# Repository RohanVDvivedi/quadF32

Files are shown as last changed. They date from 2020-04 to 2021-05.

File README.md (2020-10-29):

# Flight controller using STM32F103
[Documentation and demonstration video link](https://youtu.be/UyUF_jVTML4)

### setup requirements
(for programming stm32f103 microcontroller)

* Linux debian (to use make build system and code upload tool stm32flash)
* sublime/vi/vim/gedit any texteditor
* ARM cross compiler toolchain
  * sudo apt-get install gcc-arm-none-eabi binutils-arm-none-eabi
* stm32flash to flash the controller, assuming the controller has default factory bootloader
  * sudo apt-get install stm32flash
* stm32f103 microcontroller, with default factory bootloader (must)
* usb to uart converter
  * PL2303HX, CP2102, ftdi etc

### sensors
 * mpu6050  sccelerometer and gyroscope
 * hmc5883l magnetometer
 * ms5611 barometer

### additional accessories
 * rc transmitter and receiver

#### [STM32F10x Reference Manual](https://www.st.com/resource/en/reference_manual/cd00171190-stm32f101xx-stm32f102xx-stm32f103xx-stm32f105xx-and-stm32f107xx-advanced-arm-based-32-bit-mcus-stmicroelec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)

### connections (from microcontroller)
 * I2c1 {PB6, PB7} -> GY86 sensor {SCL, SDA}
 * UART1 {PA10, PA9} -> UART debug port {RX, TX}
 * {PB10, PB11, PB12, PB13, PB14, PB15} -> RC receiver
 * {PA0, PA1, PA2, PA3} -> PWM to ESCs of corresponding motors (Left Front, Right Front, Left Back, Right Back) of Quadcopter
 
### PCB designs
 * You will find the .sch and .brd, QuadF32 flight controller board designs in the Eagle_CAD folder.
 * It would also include a generated .cam file that I used for building my board, I would request you to use a different cam file provided by your pcb manufacturer.
 * The folder also does include .lbr library for the stm32f103 module, that I am using.

### Third party acknowledgements
 * [STM32F103-c8t6 eagle cad library](https://os.mbed.com/users/hudakz/code/STM32F103C8T6_Hello/file/accb2c83a007/mbed-STM32F103C8T6.lib/)

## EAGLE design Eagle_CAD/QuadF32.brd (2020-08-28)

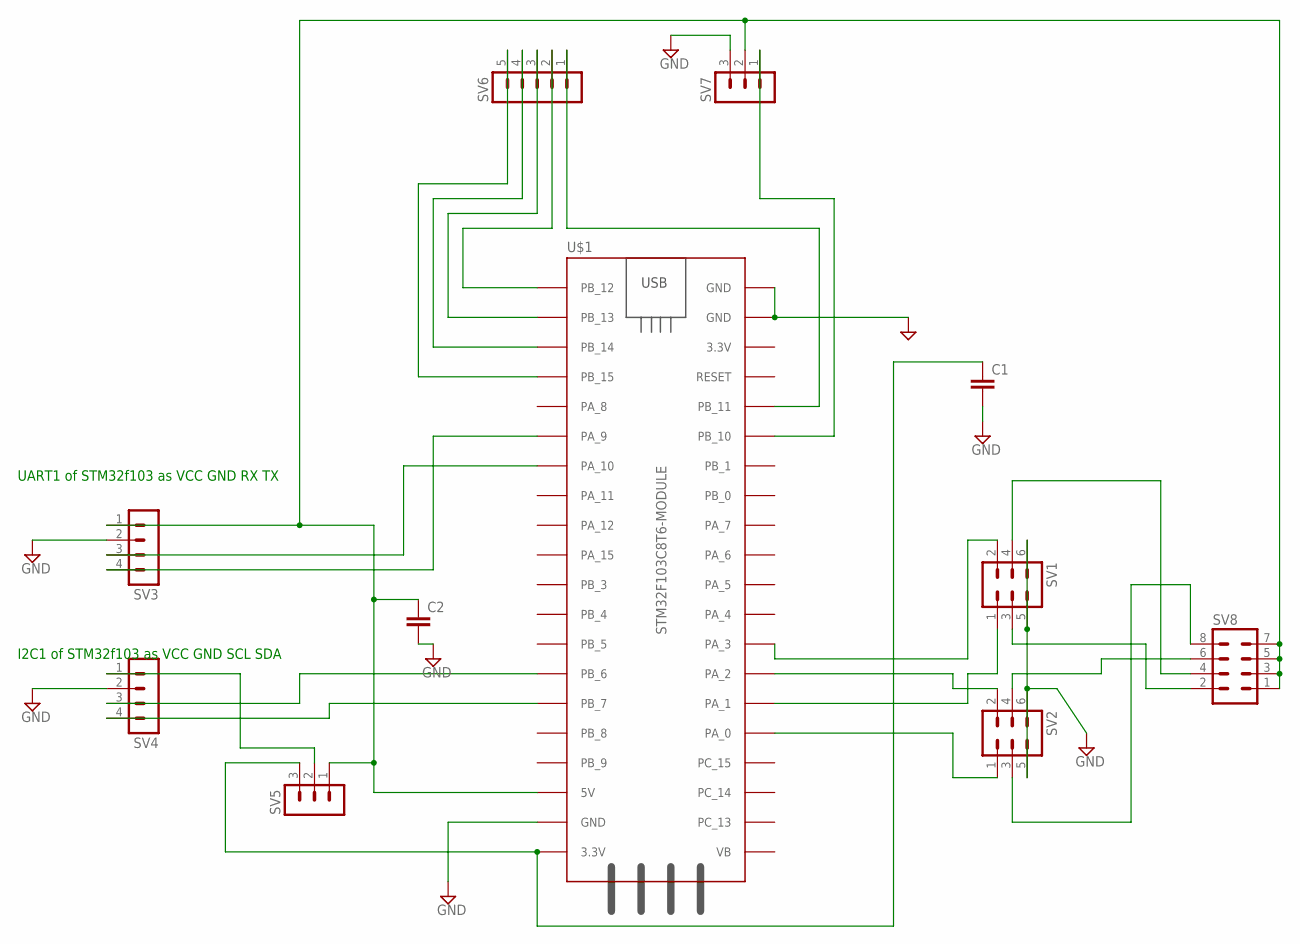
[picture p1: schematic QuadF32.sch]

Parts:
C1, C2: C5/2.5; C5B2.5
SV1, SV2: MA03-2
SV3, SV4: MA04-1
SV5, SV7: MA03-1
SV6: MA05-1
SV8: MA04-2
U$1: STM32F103C8T6-MODULE

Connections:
GND: C1.2, C2.2, SV1.5, SV1.6, SV2.5, SV2.6, SV3.2, SV4.2, SV7.3, U$1.GND_1 (GND), U$1.GND_2 (GND), U$1.GND_3 (GND)
unnamed: SV4.3, U$1.PB_6
unnamed: SV4.4, U$1.PB_7
unnamed: SV3.3, U$1.PA_10
unnamed: SV3.4, U$1.PA_9
unnamed: SV2.1, U$1.PA_0
unnamed: SV2.2, U$1.PA_2
unnamed: SV1.1, U$1.PA_1
unnamed: SV1.2, U$1.PA_3
unnamed: SV6.5, U$1.PB_15
unnamed: SV6.4, U$1.PB_14
unnamed: SV6.3, U$1.PB_13
unnamed: SV6.2, U$1.PB_12
unnamed: SV6.1, U$1.PB_11
unnamed: SV7.1, U$1.PB_10
unnamed: SV1.4, SV8.4
unnamed: C1.1, SV5.3, U$1.3.3V_1 (3.3V)
unnamed: SV4.1, SV5.2
unnamed: C2.1, SV3.1, SV5.1, SV7.2, SV8.1, SV8.3, SV8.5, SV8.7, U$1.5V
unnamed: SV2.3, SV8.8
unnamed: SV2.4, SV8.6
unnamed: SV1.3, SV8.2

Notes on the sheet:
UART1 of STM32f103 as VCC GND RX TX
I2C1 of STM32f103 as VCC GND SCL SDA

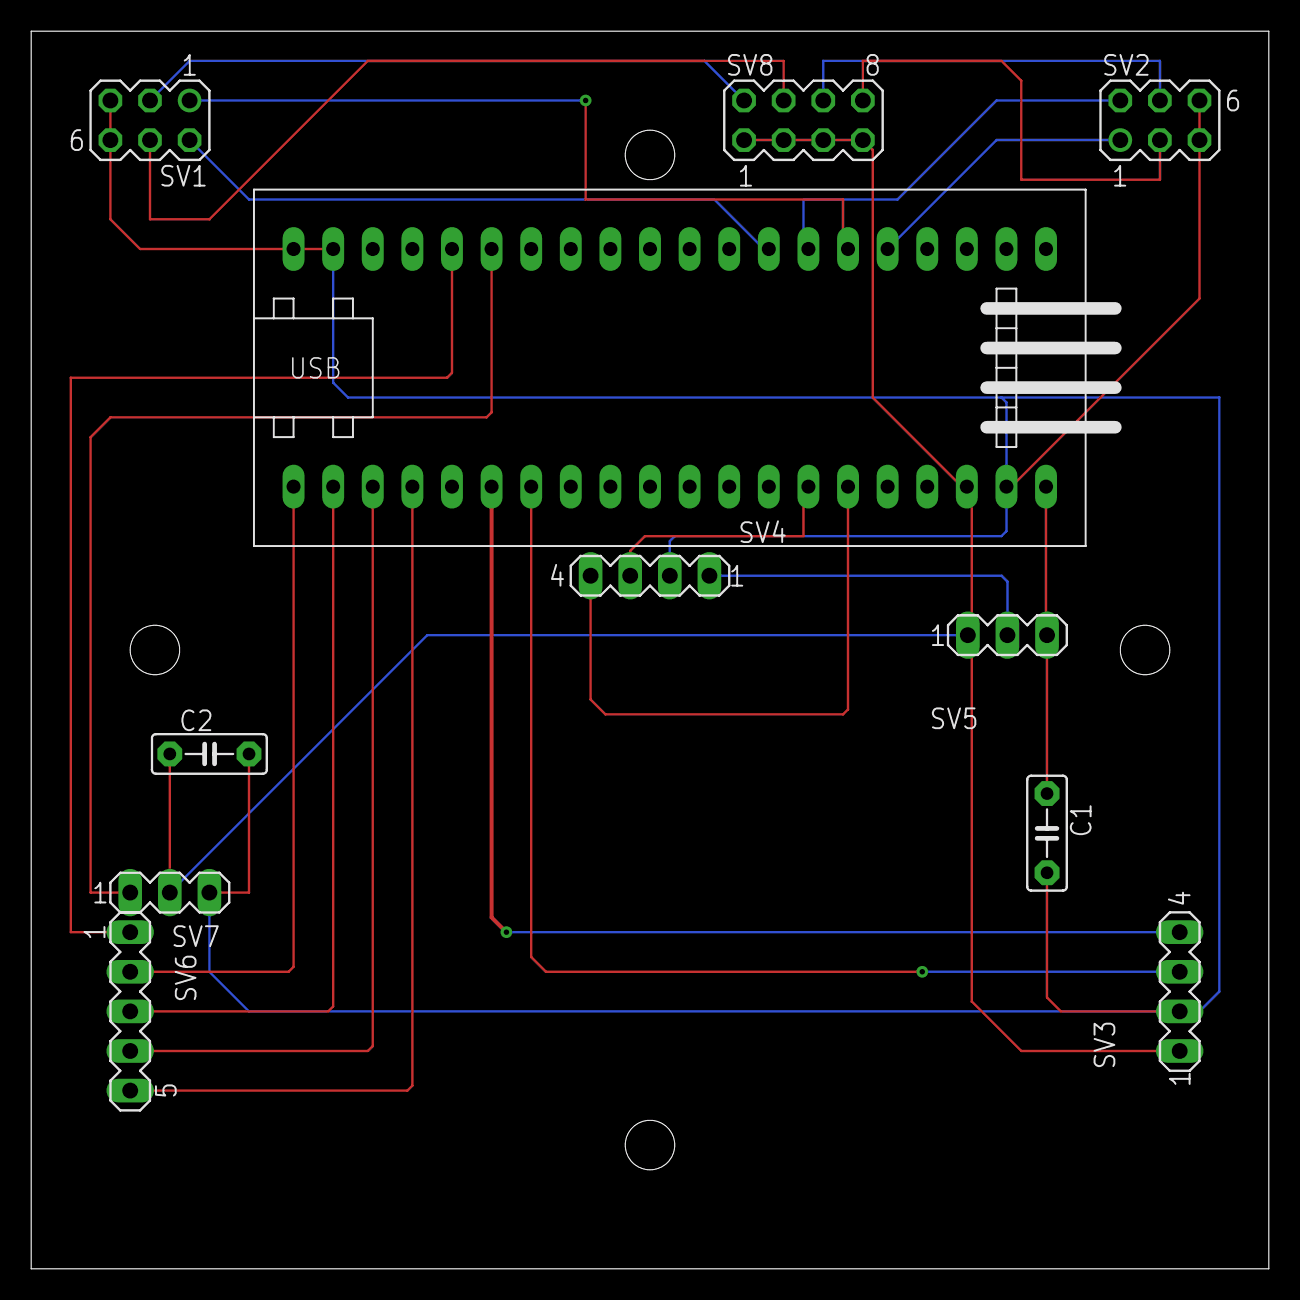
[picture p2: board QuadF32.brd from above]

Board: 2 copper layers, 79.4 x 79.4 mm, 11 parts (0 on the bottom side), 22 nets.

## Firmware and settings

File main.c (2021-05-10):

#include<delay/delay.h>
#include<d_serializer/d_serializer.h>

#include<regs/rcc.h>
#include<regs/gpio.h>

#include<sysclock/sysclock.h>
#include<uart/uart.h>
#include<i2c/i2c.h>
#include<backup_data/backup_data.h>

#include<pid/pid.h>

#include<gy86/gy86.h>
#include<bldc/quad_bldc.h>
#include<rc_receiver/rc_receiver.h>

//#define STABILIZE_MODE

#define map(val, a_min, a_max, b_min, b_max)	(b_min) + ((((float)(val)) - (a_min)) * ((b_max) - (b_min))) / ((a_max) - (a_min))

#define GYRO_ACCL_MIX     			0.98
#define LOOP_EVERY_MICROS 			2500

#define THROTTLE_MIN_VALUE			  0.0
#define THROTTLE_PID_ACTIVATE 		200.0
#define THROTTLE_MAX_VALUE			800.0

#ifdef STABILIZE_MODE
	#define ATTITUDE_INPUT_LIMIT	 30.0
#else	// it is a rate controlled quadcopter
	#define ATTITUDE_INPUT_LIMIT	120.0
#endif
#define ANGULAR_RATE_INPUT_LIMIT	120.0

#define MOTOR_MIN_PWM 				110.0
#define MOTOR_MAX_PWM 				990.0

//#define CALIBRATE_ESC_ON_START_UP

//#define DEBUG_OVER_UART
//#define PID_TO_TUNE

void main(void)
{
	// setup clock to run at 72 MHz
	change_sys_clock_source(HSE, 8000000);
	setup_pll_module(HSE, 72000000);
	change_sys_clock_source(PLL, 72000000);

	// to enable port c GPIO
	RCC->RCC_APB2ENR |= (1<<4);

	// GPIO Port C pin 13 setup as output, it is the blink led on the bluepill board
	GPIOC->GPIO_CRH &= 0xFF0FFFFF;
	GPIOC->GPIO_CRH |= 0x00200000;
	GPIOC->GPIO_ODR |= (1 << 13);

	// init rtc clock
	rtc_init();

	// setup communications
	i2c_init();
	uart_init(2000000);

	// initialize rc receiver
	init_rc_receiver();

	// initialize motors
	init_bldc();
	#if defined CALIBRATE_ESC_ON_START_UP
		set_motors(1000, 1000, 1000, 1000);
		delay_for_ms(3000);
	#endif
	set_motors(0, 0, 0, 0);

	delay_for_ms(1000);

	#if defined DEBUG_OVER_UART
		if(i2c_detect(0x68))
			uart_write_blocking("MPU detected\n", 13);
		else
			uart_write_blocking("MPU not detected\n", 17);
	#endif

	// initialize all necessary sensors
	const MPUdatascaled* mpuInit = mpu_init();

	// initialize MPUdatascaled variable used inside the loop
	MPUdatascaled mpuData = *mpuInit;

	// initialize pid variables
	// angular rate control pids, these cause differential motor corrections to attain required angular rates along local axis
		pid_state x_ang_rate_pid; pid_init(&x_ang_rate_pid, 2.7, 0.015, 0.0, 400);
		pid_state y_ang_rate_pid; pid_init(&y_ang_rate_pid, 2.7, 0.015, 0.0, 400);
		pid_state z_ang_rate_pid; pid_init(&z_ang_rate_pid, 5.4, 0.030, 0.0, 400);
	// altitude rate pid will mainly work to make 0 rate of change of altitude
		pid_state z_alt_rate_pid; pid_init(&z_alt_rate_pid, 0, 0, 0, 400);
	// flyable values
	/*
		pid_state x_ang_rate_pid; pid_init(&x_ang_rate_pid, 2.4, 0.017, 0.000030, 400);
		pid_state y_ang_rate_pid; pid_init(&y_ang_rate_pid, 2.4, 0.017, 0.000030, 400);
		pid_state z_ang_rate_pid; pid_init(&z_ang_rate_pid, 5.2, 0.037, 0.000065, 400);
	*/

	uint64_t begin_micros = get_now_micros() - LOOP_EVERY_MICROS;

	uint64_t print_iter = 0;
	char print_str[256];

	float abs_roll_init  = atanf( mpuInit->accl.yj/mpuInit->accl.zk) * 180 / M_PI;
	float abs_pitch_init = atanf(-mpuInit->accl.xi/mpuInit->accl.zk) * 180 / M_PI;

	float abs_roll  =  abs_roll_init;
	float abs_pitch = abs_pitch_init;

	float alt_rate = 0;

	while(1)
	{
		float time_delta_in_seconds = ((float)(get_now_micros() - begin_micros))/1000000.0;
		begin_micros = get_now_micros();

		GPIOC->GPIO_ODR ^= (1 << 13);

		get_scaled_MPUdata(&mpuData);

		abs_roll  = (abs_roll  + mpuData.gyro.xi * time_delta_in_seconds) * (GYRO_ACCL_MIX)
		+ (atanf( mpuData.accl.yj/mpuData.accl.zk) * 180/M_PI) * (1.0 - GYRO_ACCL_MIX);
		abs_pitch = (abs_pitch + mpuData.gyro.yj * time_delta_in_seconds) * (GYRO_ACCL_MIX)
		+ (atanf(-mpuData.accl.xi/mpuData.accl.zk) * 180/M_PI) * (1.0 - GYRO_ACCL_MIX);

		uint32_t chan_ret[6];
		int is_rc_active = get_rc_channels(chan_ret);

		float throttle = map(chan_ret[3], 0.0, 1000.0, THROTTLE_MIN_VALUE, THROTTLE_MAX_VALUE);
		float x_rc_req = map(chan_ret[5], 0.0, 1000.0, -ATTITUDE_INPUT_LIMIT, ATTITUDE_INPUT_LIMIT);
		float y_rc_req = map(chan_ret[4], 0.0, 1000.0, -ATTITUDE_INPUT_LIMIT, ATTITUDE_INPUT_LIMIT);
		float z_rc_req = map(chan_ret[2], 0.0, 1000.0, ANGULAR_RATE_INPUT_LIMIT, -ANGULAR_RATE_INPUT_LIMIT);
			chan_ret[1] = (chan_ret[1] < 3) ? 0 : chan_ret[1];
		float aux1 = map(chan_ret[1], 0.0, 1000.0, 0.0, 10.0);
			chan_ret[0] = (chan_ret[0] < 3) ? 0 : chan_ret[0];
		float aux2 = map(chan_ret[0], 0.0, 1000.0, 0.0, 40.0);

		#if defined PID_TO_TUNE
			pid_update_constants(&x_ang_rate_pid, aux1, 0.015, aux2);
			pid_update_constants(&y_ang_rate_pid, aux1, 0.015, aux2);
			//pid_update_constants(&z_ang_rate_pid, 7.0 + aux1, aux2, 0);
		#endif

		float motor_LF = throttle, motor_RF = throttle, motor_LB = throttle, motor_RB = throttle;

		#if defined STABILIZE_MODE
			float x_rate_req = aux1 * (x_rc_req - (abs_roll  -  abs_roll_init));
			float y_rate_req = aux1 * (y_rc_req - (abs_pitch - abs_pitch_init));
		#else
			float x_rate_req = x_rc_req;
			float y_rate_req = y_rc_req;
		#endif

		float z_rate_req = z_rc_req;

		if(throttle < THROTTLE_PID_ACTIVATE)
		{
			pid_reinit(&x_ang_rate_pid);
			pid_reinit(&y_ang_rate_pid);
			pid_reinit(&z_ang_rate_pid);
			pid_reinit(&z_alt_rate_pid);
		}
		else
		{
			float x_motor_corr = pid_update(&x_ang_rate_pid, mpuData.gyro.xi, x_rate_req);
			float y_motor_corr = pid_update(&y_ang_rate_pid, mpuData.gyro.yj, y_rate_req);
			float z_motor_corr = pid_update(&z_ang_rate_pid, mpuData.gyro.zk, z_rate_req);

			// we always strive to make 0 altitude rate
			float comm_motor_corr = pid_update(&z_alt_rate_pid, 0, 0);

			motor_LF += (comm_motor_corr + x_motor_corr - y_motor_corr - z_motor_corr);
			motor_RF += (comm_motor_corr - x_motor_corr - y_motor_corr + z_motor_corr);
			motor_LB += (comm_motor_corr + x_motor_corr + y_motor_corr + z_motor_corr);
			motor_RB += (comm_motor_corr - x_motor_corr + y_motor_corr - z_motor_corr);

			if(motor_LF < MOTOR_MIN_PWM)	motor_LF = MOTOR_MIN_PWM;
			if(motor_RF < MOTOR_MIN_PWM)	motor_RF = MOTOR_MIN_PWM;
			if(motor_LB < MOTOR_MIN_PWM)	motor_LB = MOTOR_MIN_PWM;
			if(motor_RB < MOTOR_MIN_PWM)	motor_RB = MOTOR_MIN_PWM;

			if(motor_LF > MOTOR_MAX_PWM)	motor_LF = MOTOR_MAX_PWM;
			if(motor_RF > MOTOR_MAX_PWM)	motor_RF = MOTOR_MAX_PWM;
			if(motor_LB > MOTOR_MAX_PWM)	motor_LB = MOTOR_MAX_PWM;
			if(motor_RB > MOTOR_MAX_PWM)	motor_RB = MOTOR_MAX_PWM;
		}

		set_motors(motor_LF, motor_RF, motor_LB, motor_RB);

		#if defined DEBUG_OVER_UART
			if(print_iter == 100)
			{
				print_iter = 0;

				char* end_ps = print_str;

				//end_ps = stringify_integer(end_ps, is_rc_active); *end_ps = ' '; end_ps++; *end_ps = '\t'; end_ps++;

				//end_ps = stringify_integer(end_ps, motor_LF); *end_ps = ' '; end_ps++; *end_ps = '\t'; end_ps++;
				//end_ps = stringify_integer(end_ps, motor_RF); *end_ps = ' '; end_ps++; *end_ps = '\t'; end_ps++;
				//end_ps = stringify_integer(end_ps, motor_LB); *end_ps = ' '; end_ps++; *end_ps = '\t'; end_ps++;
				//end_ps = stringify_integer(end_ps, motor_RB); *end_ps = ' '; end_ps++; *end_ps = '\t'; end_ps++;

				end_ps = stringify_float(end_ps, aux1); *end_ps = ' '; end_ps++; *end_ps = '\t'; end_ps++;
				end_ps = stringify_float(end_ps, aux2); *end_ps = ' '; end_ps++; *end_ps = '\t'; end_ps++;

				//end_ps = stringify_integer(end_ps, chan_ret[0]); *end_ps = ' '; end_ps++; *end_ps = '\t'; end_ps++;
				//end_ps = stringify_integer(end_ps, chan_ret[1]); *end_ps = ' '; end_ps++; *end_ps = '\t'; end_ps++;
				//end_ps = stringify_integer(end_ps, chan_ret[2]); *end_ps = ' '; end_ps++; *end_ps = '\t'; end_ps++;
				//end_ps = stringify_integer(end_ps, chan_ret[3]); *end_ps = ' '; end_ps++; *end_ps = '\t'; end_ps++;
				//end_ps = stringify_integer(end_ps, chan_ret[4]); *end_ps = ' '; end_ps++; *end_ps = '\t'; end_ps++;
				//end_ps = stringify_integer(end_ps, chan_ret[5]); *end_ps = ' '; end_ps++; *end_ps = '\t'; end_ps++;

				//end_ps = stringify_float(end_ps, x_ang_rate_pid.constants.Kp); *end_ps = ' '; end_ps++; *end_ps = '\t'; end_ps++;
				//end_ps = stringify_float(end_ps, x_ang_rate_pid.constants.Ki); *end_ps = ' '; end_ps++; *end_ps = '\t'; end_ps++;
				//end_ps = stringify_float(end_ps, x_ang_rate_pid.constants.Kd); *end_ps = ' '; end_ps++; *end_ps = '\t'; end_ps++;

				//end_ps = stringify_float(end_ps, y_ang_rate_pid.constants.Kp); *end_ps = ' '; end_ps++; *end_ps = '\t'; end_ps++;
				//end_ps = stringify_float(end_ps, y_ang_rate_pid.constants.Ki); *end_ps = ' '; end_ps++; *end_ps = '\t'; end_ps++;
				//end_ps = stringify_float(end_ps, y_ang_rate_pid.constants.Kd); *end_ps = ' '; end_ps++; *end_ps = '\t'; end_ps++;

				//end_ps = stringify_float(end_ps, z_ang_rate_pid.constants.Kp); *end_ps = ' '; end_ps++; *end_ps = '\t'; end_ps++;
				//end_ps = stringify_float(end_ps, z_ang_rate_pid.constants.Ki); *end_ps = ' '; end_ps++; *end_ps = '\t'; end_ps++;
				//end_ps = stringify_float(end_ps, z_ang_rate_pid.constants.Kd); *end_ps = ' '; end_ps++; *end_ps = '\t'; end_ps++;

				//end_ps = stringify_float(end_ps, mpuData.gyro.xi); *end_ps = ' '; end_ps++; *end_ps = '\t'; end_ps++;
				//end_ps = stringify_float(end_ps, mpuData.gyro.yj); *end_ps = ' '; end_ps++; *end_ps = '\t'; end_ps++;
				//end_ps = stringify_float(end_ps, mpuData.gyro.zk); *end_ps = ' '; end_ps++; *end_ps = '\t'; end_ps++;

				//end_ps = stringify_float(end_ps, mpuInit->gyro.xi); *end_ps = ' '; end_ps++; *end_ps = '\t'; end_ps++;
				//end_ps = stringify_float(end_ps, mpuInit->gyro.yj); *end_ps = ' '; end_ps++; *end_ps = '\t'; end_ps++;
				//end_ps = stringify_float(end_ps, mpuInit->gyro.zk); *end_ps = ' '; end_ps++; *end_ps = '\t'; end_ps++;

				//end_ps = stringify_float(end_ps, mpuData.accl.xi); *end_ps = ' '; end_ps++; *end_ps = '\t'; end_ps++;
				//end_ps = stringify_float(end_ps, mpuData.accl.yj); *end_ps = ' '; end_ps++; *end_ps = '\t'; end_ps++;
				//end_ps = stringify_float(end_ps, mpuData.accl.zk); *end_ps = ' '; end_ps++; *end_ps = '\t'; end_ps++;

				//end_ps = stringify_float(end_ps, mpuInit->accl.xi); *end_ps = ' '; end_ps++; *end_ps = '\t'; end_ps++;
				//end_ps = stringify_float(end_ps, mpuInit->accl.yj); *end_ps = ' '; end_ps++; *end_ps = '\t'; end_ps++;
				//end_ps = stringify_float(end_ps, mpuInit->accl.zk); *end_ps = ' '; end_ps++; *end_ps = '\t'; end_ps++;

				//end_ps = stringify_float(end_ps, abs_roll); *end_ps = ' '; end_ps++; *end_ps = '\t'; end_ps++;
				//end_ps = stringify_float(end_ps, abs_pitch); *end_ps = ' '; end_ps++; *end_ps = '\t'; end_ps++;

				//end_ps = stringify_float(end_ps, x_rc_req); *end_ps = ' '; end_ps++; *end_ps = '\t'; end_ps++;
				//end_ps = stringify_float(end_ps, y_rc_req); *end_ps = ' '; end_ps++; *end_ps = '\t'; end_ps++;

				//end_ps = stringify_float(end_ps, x_rate_req); *end_ps = ' '; end_ps++; *end_ps = '\t'; end_ps++;
				//end_ps = stringify_float(end_ps, y_rate_req); *end_ps = ' '; end_ps++; *end_ps = '\t'; end_ps++;
				
				//end_ps = stringify_float(end_ps, time_delta_in_seconds); *end_ps = ' '; end_ps++; *end_ps = '\t'; end_ps++;

				*end_ps = '\n'; end_ps++;
				uart_write_through_dma(print_str, end_ps - print_str);
			}
			else
				print_iter++;
		#endif

		delay_until_us(begin_micros + LOOP_EVERY_MICROS);
	}
}

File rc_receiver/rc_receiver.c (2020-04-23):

#include<rc_receiver/rc_receiver.h>

// channel_start with -1 means it is uninitialized or had an error in last read
static volatile uint32_t channel_start[6];
static volatile uint32_t channel_value[6];

// it stores the last microsecond time, when the rc receiver actively provided values
static volatile uint64_t last_rc_value_micros = 0;

void edge_interrupt_rc_channel(void);

#define VECTOR_TABLE_ENTRY_POSITION_EXTI_10_15 		40
#define VECTOR_TABLE_BASE	((volatile uint32_t*)(0x08000040))
#define EXTI_10_15_VECTOR_TABLE_ENTRY_REFERENCE  	((volatile uint32_t*)(VECTOR_TABLE_BASE + VECTOR_TABLE_ENTRY_POSITION_EXTI_10_15))

void init_rc_receiver()
{
	// turn on timer 5 clock and the PB10-PB15 pins ports clocks
	// since we are using alternate functions i.e. interrupts from port B, turn on afio clock
	RCC->RCC_APB1ENR |= (1<<2);
	RCC->RCC_APB2ENR |= ((1<<3) | (1<<0));

	// setup timer 5 ticking every microsecond
	TIM4->TIM_CR1 = 0;
	TIM4->TIM_SMCR = 0;
	TIM4->TIM_CNT = 0;
	TIM4->TIM_PSC = 71;
	TIM4->TIM_ARR = 65535;
	TIM4->TIM_CR1 |= (1<<0);

	// setup gpio to input mode, and configure them to use as input to EXTI interrupt module
	GPIOB->GPIO_CRH = (GPIOB->GPIO_CRH & ~(0xffffff00)) | 0x88888800;
	AFIO->AFIO_EXTICR3 = 0x00001100;
	AFIO->AFIO_EXTICR4 = 0x00001111;

	// setup six interrupts on the port
	int channel_no;
	for(channel_no = 0; channel_no < 6; channel_no++)
	{
		int channel_pin = channel_no + 10;

		EXTI->EXTI_IMR  |= (1<<channel_pin);
		EXTI->EXTI_RTSR |= (1<<channel_pin);
		EXTI->EXTI_FTSR |= (1<<channel_pin);

		GPIOB->GPIO_ODR &= ~(1<<channel_pin);
	}

	// setting up NVIC controller registers
	//(*((volatile uint32_t*)(EXTI_10_15_VECTOR_TABLE_ENTRY_REFERENCE))) = ((uint32_t)(edge_interrupt_rc_channel));
	NVIC->NVIC_ISER[1] |= (1<<(VECTOR_TABLE_ENTRY_POSITION_EXTI_10_15-32));
}

void update_rc_channel(int channel_no)
{
	uint32_t timer_counter_value = TIM4->TIM_CNT;
	int channel_pin = channel_no + 10;
	if(GPIOB->GPIO_IDR & (1<<channel_pin))
	{
		channel_start[channel_no] = timer_counter_value;
	}
	else if(timer_counter_value > channel_start[channel_no])
	{
		channel_value[channel_no] = timer_counter_value - channel_start[channel_no];
	}
}

void edge_interrupt_rc_channel(void)
{
	uint32_t TIMR4_value = TIM4->TIM_CNT;
	uint32_t GPIOB_value = GPIOB->GPIO_IDR;
	uint32_t EXTI_PR_val = EXTI->EXTI_PR;

	uint32_t clear_pending = 0;

	int channel_no;
	int channel_pin;
	for(channel_no = 0; channel_no < 6; channel_no++)
	{
		channel_pin = channel_no + 10;
		if(EXTI_PR_val & (1<<channel_pin))
		{
			if(GPIOB_value & (1<<channel_pin))
			{
				channel_start[channel_no] = TIMR4_value;
			}
			else if(TIMR4_value > channel_start[channel_no])
			{
				channel_value[channel_no] = TIMR4_value - channel_start[channel_no];
			}
			else
			{
				channel_value[channel_no] = TIMR4_value + 65536 - channel_start[channel_no];
			}
			clear_pending |= (1<<channel_pin);
		}
	}

	EXTI->EXTI_PR |= clear_pending;
	NVIC->NVIC_ICPR[1] |= (1<<(VECTOR_TABLE_ENTRY_POSITION_EXTI_10_15-32));

	last_rc_value_micros = get_now_micros();
}

static uint32_t compare_and_map_and_range(uint32_t value)
{
	if(value < 1000)
	{
		value = 1000;
	}
	else if(value > 2000)
	{
		value = 2000;
	}
	value = value - 1000;
	return value;
}

int get_rc_channels(uint32_t chan_ret[6])
{
	// if no rc receiver interrupt is generated in past 50 ms, we mark that the rc receiver is inactive
	int is_rc_receiver_active = 1;
	if((get_now_micros() - last_rc_value_micros > 50000) || (last_rc_value_micros == 0))
	{
		is_rc_receiver_active = 0;
	}

	int iter_ch;
	for(iter_ch = 0; iter_ch < 6; iter_ch++)
	{
		chan_ret[iter_ch] = is_rc_receiver_active ? compare_and_map_and_range(channel_value[iter_ch]) : 0;
	}

	return is_rc_receiver_active;
}

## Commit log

2020-03-21 added sources for handling DMA got supporting i2c and usart
2020-03-21 building up the uart source, still in progress
2020-03-21 USART setup done - not working :(
    [main.c, uart.c]
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2020-03-21 USART works and enough confidence to develop anything baremetal, made worlds worst mistake using macros for stuff for which structus are required
    [main.c, uart.c]
2020-03-22 using RCC registers from regs/usart only and uart initilized to use buadrate provided to it from uart_init parameters
2020-03-23 removed DMA header and source, we will only keep the source of DMA access separate and different to each requirement
2020-03-23 building separate definitions for dma and blocking access for uart writes
2020-03-23 DMA registers header and the test program setup
2020-03-23 done development for dma, but the transfer not working
    [main.c, uart.c]
2020-03-23 only changed ordering of the registers setup in DMA
2020-03-23 Bare metal uart DMA working, DMA shows significant improvement on the CPU usage by offloading io on DMA great thing to learn by experience, next time, we hit delay functions in the nuts and instead u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
2020-03-24 can cnahe from HSE to HSI, but not able to use PLL, flash and peripheral buses are setup accordingly, functions to get clock source or frequency setup correctly
    [main.c, uart.c]
2020-03-24 program reports its current clock frequency, no improvement still pll clock is not getting enabled
2020-03-24 corrected the frequenccy finding logic and uart works
    [main.c, uart.c]
2020-03-24 started development for i2c, timers will be next
2020-03-25 added statements to turn on the i2c 1, setup GPIO ports and changed functon discriptions that will help us build over for different sensors
2020-03-25 implemented blocking function for i2c, not tested, I am sure they are going to be bugy
    [i2c.c]
2020-03-25 few errors in implementation of i2c cleared
    [i2c.c]
2020-03-25 built a small storage 8 bytes, a base line for funtioning of i2c tests
2020-03-25 few errors resolved, test program setup to handle i2c io
    [i2c.c, main.c]
2020-03-25 we do not mess with anything beyond address write on the i2c bus, if bytes for io are 0
2020-03-26 a lot of debug code still litters in i2c i2c driver not built yet, need a lot of time to work
2020-03-26 i2c lines are getting driven by master stm32 bug win
    [i2c.c, main.c]
2020-03-26 most issues resolved, driver io
    [i2c.c, main.c]
2020-03-26 test ans try the write portion of the driver
2020-03-26 read and write all working cool, for atleast 1 byte, larger byte io and dma with i2c are next goals
2020-03-26 built completely functional test code for i2c driver, works flawlessly
2020-03-26 due to the nature of the program, we need blocking writes to uart, i2c device address can now be changed
2020-03-27 final nail in the i2c master driver of stm32, fully functional, for register address and data based sensors, plain format or command based protocols example the one used by barometer sensors need few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
2020-03-30 made i2c to work at 400KHz with sysclock running at 72MHz
2020-03-31 added timer registers that wil be used to drive bldc motors for the quadcopter
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2020-03-31 need to add registers and configuration rebuilding because we will have to use a similar timer 2, instead of timer 1
2020-04-01 since all the registers for all the timers are idnetically structures, we club all of them as just timers
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2020-04-01 using timer 2 instead of 1 for the bldc, this is just because of board compatibility
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2020-04-01 added and trying to amke and test timer2 with bldc, but not working
    [main.c, quad_bldc.c]
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2020-04-03 added logic to use timer 3 for receiving data from rc channe;
2020-04-04 using traditional style interrupt based any pin rc receiver captre, istead t of my new idea of relying solely on timer input captures
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2020-04-05 added logic to check if the given pin created the external interrupt, also a minor bug resolved
    [rc_receiver.c]
2020-04-05 using afio module to alter interrupt pins from port a to port b and interrupts enabled
2020-04-05 nvic and rcreceiver interrupts enabled, but the stuff is not set properly
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2020-04-05 corrected pointer arithmethic for calculating the offset to EXTI10-15 interrupts
    [rc_receiver.c]
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2020-04-05 rc receiver NVIC not working
    [rc_receiver.c]
2020-04-05 removed debug logic, corrected minute errors, and cleared old debug tangled code
    [main.c, rc_receiver.c]
2020-04-05 TImer 5 that was being used for the rc_receiver is not working
    [main.c, rc_receiver.c]
2020-04-05 forgot stm32f103 has only 4 counters, and I was using TIM5 :P xD
2020-04-06 modularizing the rc_receiver code. bug -> it accepts only one channel as input from all 6 ones, i.e. outof 6 channels if 2,3,5 are connected it will only pick the lowest channel the 2nd one, need to 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
    [rc_receiver.c]
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2020-04-15 copied all the required logic from quadf for picking up sensor data
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2020-04-17 altered main and removed errors, setup built to setup the rtc clock
    [main.c]
2020-04-17 going by the rules of the datasheet we need to return and check the missing points that we skipped in over confidence :p
    [main.c]
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2020-04-17 minor change printing z axis valies since a good serializer logic is not avalable in the project
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2020-04-23 minor bug resolved in stringify double
    [main.c]
2020-04-23 mapped and corrected rc input values
    [main.c]
2020-04-23 minor bug in the directiion resolved
    [main.c]
2020-04-23 added protection against out of bound motor values
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2020-04-30 made the flight controller completely tunable, removing all the unnecesary logic from the updating pid constants, clearing logic as required
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2020-05-02 error with motor directions
    [main.c]
2020-05-02 changing the aux limits for PI gains, motor directiond for x and y axis are correct
    [main.c]
2020-05-03 removing redundant delay and setting aux2 to 0 to test the bug
    [main.c]
2020-05-07 added macros to help calibrating ESCs on startup
2020-06-11 z direction correction chekc after adding new motors
    [main.c]
2020-06-14 tested x axis with same values as y and tests passed
2020-06-15 added functionality for calculating absolute roll and pitch for the controller
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2020-06-18 increasing the pid limits to get better coverng
2020-06-20 3.5 is a pid controller saturation limit for the pid controller in the given testcase
2020-06-20 minor oscillations but the results are great
    [main.c]
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2020-06-20 very slow control over drone, reducing the p gain surely helped with overshooting motor
    [main.c]
2020-06-20 using z required for rate control with the same pid values as pitch and roll axis
2020-06-20 baack to square 1, having the same pid tuning as the old copter
2020-06-21 Pitch and roll axis pid values tuned very well
2020-06-22 pid propotional z axis gain is now flyable on atleast the indoor test bench
2020-06-22 defining throttle min and max values to be written when pid is activated or not
2020-06-22 better indoors stability results by increasing I gain
    [main.c]
2020-06-23 incresing sensitivilty tto controll by redung insensitivity limits in x, y axis
2020-06-23 increased I gain shows higher stability and teadiness in the inner faster loop, reducing outer slow pid p gain to reduce oscillations
    [main.c]
2020-06-23 there can not be better rate pid values
2020-06-23 rate pid made softer to accomodate room for variations given by angle controller
2020-06-23 yaw pid tuned and snce the values have been almost double, of the rate pid of pitch and roll axis, they have also been made the same
2020-06-23 development for futher adding altitude rate controller, and the only propotional controller now is a full fledged pid controller
2020-06-24 reducing p and d gains to get rid of oscillations completely, but the response has become smooth now
    [main.c]
2020-06-24 using slowly stabilize as required mode
    [main.c]
2020-06-24 the logic of initial roll and pitch separated and performed only initialy, so as to reduce online computation asweell as check its effect on the syatem
2020-07-17 make file upgraded, starup code fixated to use main as the _start function
    [main.c]
2020-07-17 missing flags architecture flags
    [main.c]
2020-08-28 added eagle cad files for board to the project
    [QuadF32.brd, QuadF32.sch]
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2020-10-27 increasing input ranges and a teensy bit of d gain for reducing oscillations on fast stick releases
    [main.c]
2020-10-27 yaw control just can not be better - alttitude controll is the next
2020-10-28 none change- ESC issues so need higher D gain on attitude rate
    [main.c]
2020-10-30 initialing rate values bug fixed, stringify float bug fixed
    [main.c]
2020-10-30 good enough gains for maneuvering, but oscillates
    [main.c]
2020-10-30 need to debug rc receiver errors in values recevived on controller reset
    [main.c]
2020-10-31 lowered d-gain, but very small oscillations, little lesser i gain is still working, yet very fast maneuvering is not possible yet
    [main.c]
2020-11-01 better faster yaw control, smoother and faster attitude, -> oscillations disappear, still P gain feels lighter on attitude and can be increased -> finally it would be better to add angle stab control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
    [main.c]
2020-11-02 lowered all d gains for fast maneuvers, slight oscillations on fast stick movements
    [main.c]
2020-11-06 updated tuning constants PD or rate gain, to allow higher P with a bit more oscillations and altitude gain, this enables for a better angle controller tuning
    [main.c]
2020-11-08 updated gains after retuning rate gains mainly reducing d gains for stab gains issue
    [main.c]
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2021-03-27 using initializaion abs roll and pitch values to fix the fixed initial attitude
    [main.c]
2021-03-27 fix in using macro for STAB PID
    [main.c]
